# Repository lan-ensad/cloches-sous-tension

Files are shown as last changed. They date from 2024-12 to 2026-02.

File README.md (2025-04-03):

# cloches sous tensions

<!-- TOC -->
- [1. How it works](#1-how-it-works)
    - [1.1. General hardware diagram](#11-general-hardware-diagram)
    - [1.2. General software diagram](#12-general-software-diagram)
- [2. Programm usage](#2-programm-usage)
    - [2.1. Two modes](#21-two-modes)
    - [2.2. Config.yaml](#22-configyaml)
    - [2.3. Class & Functions](#23-class--functions)
        - [2.3.1. sol](#231-sol)
        - [2.3.2. recorder](#232-recorder)
        - [2.3.3. player](#233-player)
        - [2.3.4. utils](#234-utils)
- [3. Electronic](#3-electronic)
    - [3.1. Components](#31-components)
    - [3.2. PCB layout](#32-pcb-layout)
    - [3.3. Wiring](#33-wiring)
- [4. MIDI hardaware](#4-midi-hardaware)
- [5. 3D Modeling](#5-3d-modeling)
- [6. Non-tested modifications](#6-non-tested-modifications)
- [7. Known bugs](#7-known-bugs)
- [8. V2 expected](#8-v2-expected)
- [9. Maintenance, update](#9-maintenance-update)
- [10. Hardware limitations](#10-hardware-limitations)
<!-- /TOC -->

***

This project was born in collab with [Francois Dufeil](https://francoisdufeil.com/) and his sculptural works. 

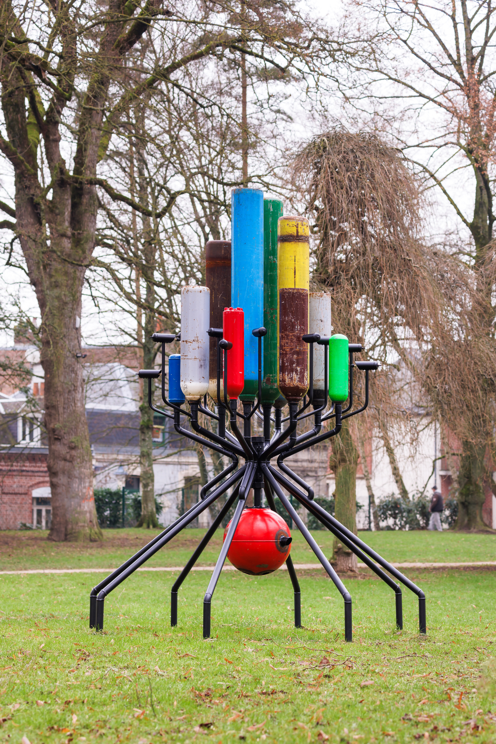
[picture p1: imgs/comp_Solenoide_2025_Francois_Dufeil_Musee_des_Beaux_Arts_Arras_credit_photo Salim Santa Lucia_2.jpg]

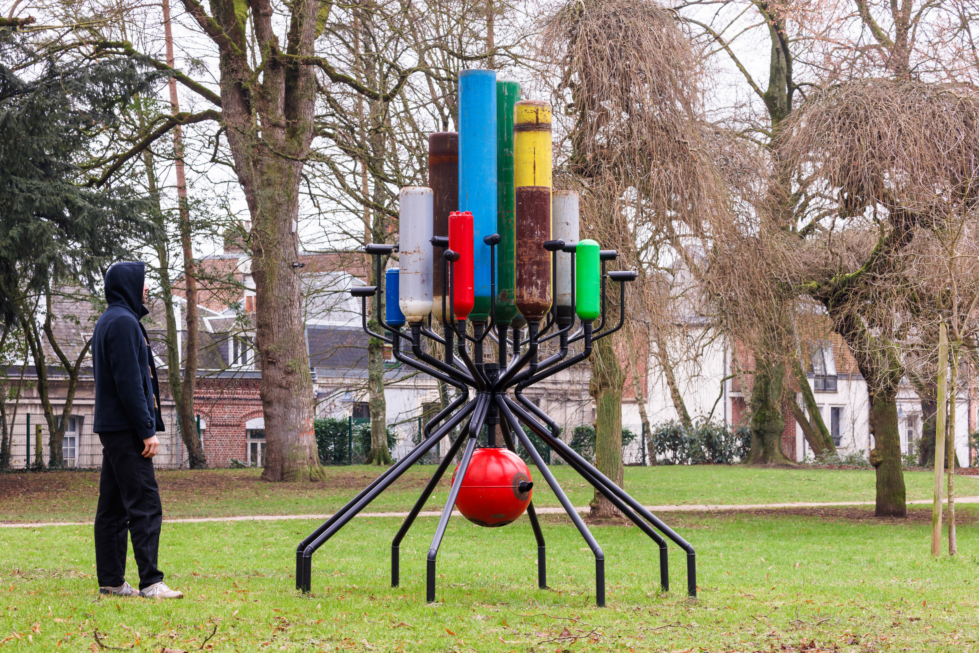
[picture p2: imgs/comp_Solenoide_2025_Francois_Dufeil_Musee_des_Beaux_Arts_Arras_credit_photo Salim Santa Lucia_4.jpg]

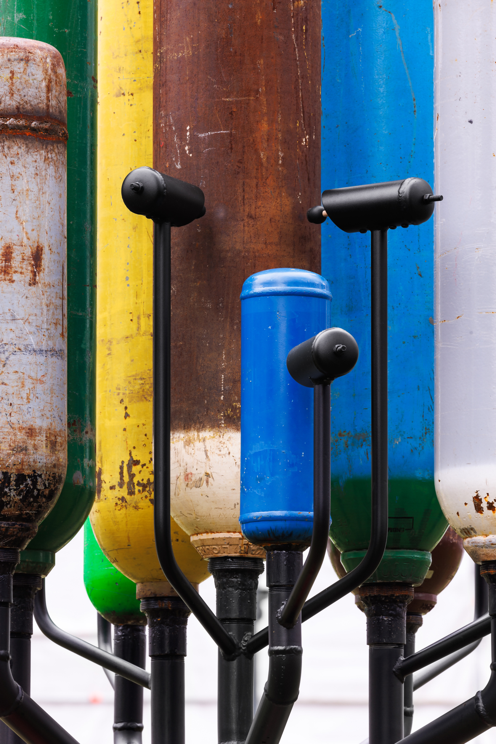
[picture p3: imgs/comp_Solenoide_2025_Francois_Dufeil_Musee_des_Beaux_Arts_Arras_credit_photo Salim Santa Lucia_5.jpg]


**Video :**\
video (https://www.youtube.com/watch?v=u8s93TluLmw)

photo @[Salim Santa Lucia](http://salimsantalucia.com/)

It uses a raspberry PCA9685 shield and 16 solenoides ITS-LS3830BD and homemade pcbs with a mosfet type IRL540. The goal is control accuratly the velocity of the impact between motors and bells to be able to play *forte* and *piano*.

Python main script runs `@reboot` in the `crontab` system.

## 1. How it works

### 1.1. General hardware diagram

hardware

### 1.2. General software diagram

software

## 2. Programm usage

### 2.1. Two modes

- **live** 
    - activate solenoides with a midi crontoller
    - in `config.yaml` you can set :
        - `message.note`\
            to map the midi note of the controller
        - `message.velocity`\
            it use the velocity to trigg the mosfet
        - record a score. Note that the score is not recorded in .midi but in .txt (cf.[Class & Functions](#class--functions)>**recorder**)
        - `message.control_change`\
            to map the control_change note (cf.[Class & Functions](#class--functions)>**`toggle_drony()`**)
    - for the happening \
    more details : [MIDI hardware](#midi-hardaware)
        - Arturia KeyStep Pro → MIDI out
        - MIDI in → Arturia BeatStep Pro
    - do not care about `message.channel` or `message.time`
- **auto**
    - read a score at the boot (cf.[Class & Functions](#class--functions)>**utils**>**`draw_lottery()`** and **`many_lottery()`**)
    - in `config.yaml` `date` where can set the range and the number of `draw_lottery()` defines in `utils.py`
    - when auto mode is triggered, `handle_score()` will read at once a score. After the `first_playing_score` is set to False and the function wait `now() == target()` to read the next score store in table_draw
    - `table_draw` is define with the `utils.many_draw(x)` function where x is the number of auto will be triggered

### 2.2. Config.yaml

|function|description|
|--|--|
|**controller**|simply the name of the controller. You can use `available_ports()` function in `utils.py` to get the exacte name.|
|**date**|usefull to set the range of hours to trigger the automation, the number of time of activation|
|**signal**|define the range of value (7bits for midi input and 16bits for PWM signal) and sommes default value when drony is triggered|
|**PWM**|settings for the PCA9685 shield|
|**mapping**|collection of midi notes and control_change to map the PWM channel of the PCA9685|
|**machine**|specifications of the machine (motors, btn_pin, led_pin) AND the `travel_time` table wich defines the `hit_length` of solenoides depending of the `message.velocity`|

### 2.3. Class & Functions

#### 2.3.1. sol

Main class based on asyncio

|function|description|
|--|--|
|**tape()**|It automaticly set the travel_time `self.hit_length` by searching in the config.yaml at machine->motors->travel_time| 
|**toggle_drony()**|When call, it create an async task `self.drony()` or cancels it if `self.dronying` is True. It free some bandwith for the midi signal and you can set the time between two tapes with the `midi.control_change.value` into the `stream_potard()`|
|**drony()**|**Do not call by itself**. The security heat setting is comments, ad the frequency calculator. the `self.delai_off` is set with the `self.stream_potar()` function|
|**get_timer()**|It uses by security settings as well as frequency calculator|

#### 2.3.2. recorder

|function|description|
|--|--|
|**get_current_millis()**|the recorder needs to know the duration between two midi note. Only 1ms definition|
|**write()** and **record()**|realy simple and automated. You can call the `rec.record_score()` in each loop, it will record as the `rec.record_status == True` and stop when is False.|

You can take a look at the `handle_score()` in `main.py` or `recorder.py`.

This is a sample of recorder looks like :
```
450
note_on channel=0 note=67 velocity=40 time=0
106
note_off channel=0 note=67 velocity=64 time=0
387
note_on channel=0 note=68 velocity=100 time=0
```
#### 2.3.3. player

|function|description|
|--|--|
|**read_file()**|load a score in `self.raws`|
|**parse_midi_string()**|use the mido `Message()` function to return the line's score into a midi message|

The `handle_score()` in `main.py` parse the file line by line to consider odds line with the delay between to midi messages.

#### 2.3.4. utils
Collection of functions

|function|description|
|--|--|
|**pca**|Usefull to use the driver just by calling `utils.pca.*<any_functions>*`|
|**draw_lottery()** and **many_lottery()**|Theses functions read how many `.txt` are in the root folder to set the table_draw list|
|**reset_all_pwn()**|Pretty secure to avoid any locked in solenoide at every boot|
|**available_ports()**|You can know the exacte name of your midi controller|
|**connecting_controller()**|Async function to let user switch the machine state before or after the keyboard pluged|

## 3. Electronic

### 3.1. Components

- RaspberryPi 4 with a [PCA9685 shield](https://www.waveshare.com/wiki/Fan_HAT)\
I only use it for the PCA9685 chip controlled I2C
    - installation
    ```
    sudo apt update && sudo apt upgrade
    sudo apt install python3-pip python3-smbus
    sudo pip install RPi.GPIO
    ```
- [Button](https://www.gotronic.fr/art-bouton-poussoir-ip67-bt22b-l-v-34105.htm) to switch live/auto mode
- [Emergency stop button](https://www.amazon.fr/gp/product/B097B8S6XL/ref=ox_sc_act_title_1?smid=A066248065M1IW1TJ2D&psc=1) connect only on the 48Volt power supply
- 12V and 48V power supply. 12V for the Raspberry and 48V (we chose 420W) for the solenoides.

### 3.2. PCB layout

You can find the KiCad projet, .svg and .step in `pcb_design/_src` folder. I chose the irl540 mosfet to design the regulator. 

- Schem
schem

- Layout
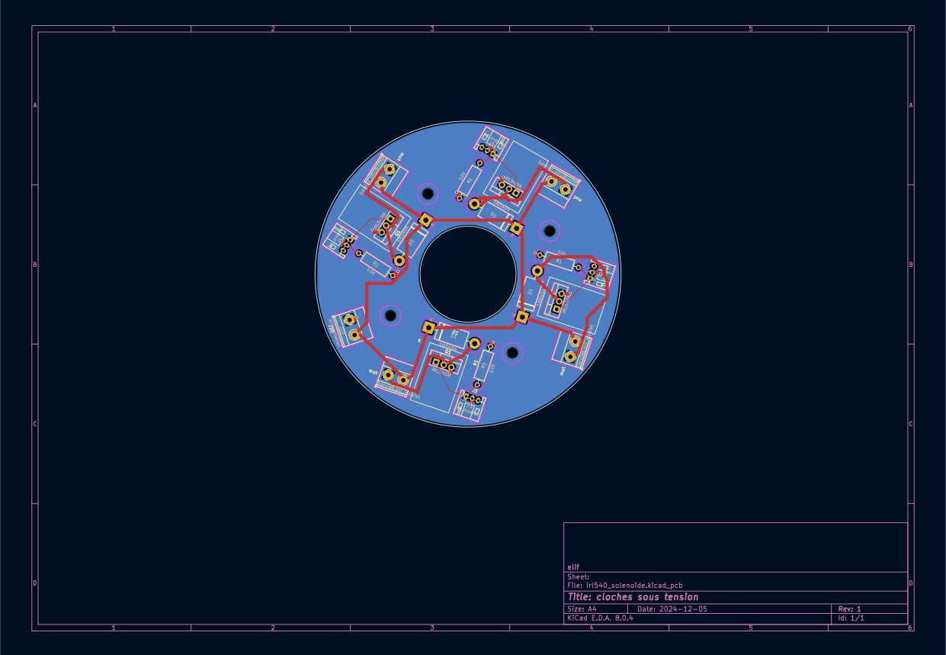
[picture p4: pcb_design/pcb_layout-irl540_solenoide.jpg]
layout

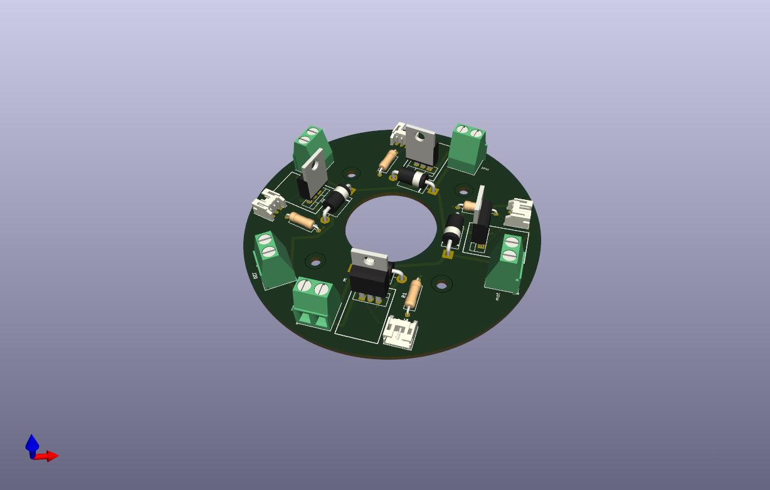
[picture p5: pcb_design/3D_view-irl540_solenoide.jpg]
schem


### 3.3. Wiring

- 16 pwm output from the pca9685 shield on the irl540 pcb with the common rapsberry and shield GND
- button\
you can find all in `config.yaml`:`machine`
    - GPIO27 : pullup pin
    - GPIO17 : led pin
    - the GND is common

wiring

## 4. MIDI hardaware

- [BeatStep Pro](https://www.arturia.com/fr/products/hybrid-synths/beatstep-pro/resources) made by Arturia. This is the master keyboard connected to the Raspberry Pi. You can download the Midi Control Center to map all the keys and match it in `config.yaml`.
- [KeyStop Pro](https://www.arturia.com/fr/products/hybrid-synths/keystep-pro/resources) made by Arturia. We use it to send midi notes and play with all the features — record sequences, arpeggiators, pattern, scaling, arranging... — This keyboard is really easy to use and very versatil.

keyboad-connections

## 5. 3D Modeling

You can find some parts that we use to properly mount the brain inside the box.

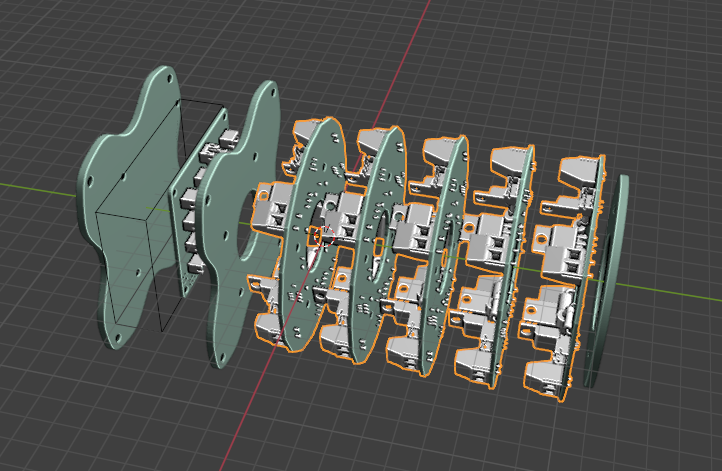
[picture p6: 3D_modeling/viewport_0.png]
viewport


## 6. Non-tested modifications

- time-mapping in microsecond instead milliseconds
    - drasticly reduce the queue time
    - more convient with live mode and recording mode
- disable the first delay in the recorder
- change toggle_drony() to activate_drony() and stop_drony()\
    more stable and accurate to the note_on or note_off midi signal

## 7. Known bugs

- sometimes the recorder apply a 10 or 100 factore to the delay between two midi signal

## 8. V2 expected

- add redis server to catch and possibly change some values
- add logging
- separate all functions
    - live
    - routine
    - reading
- add node-red interface
    - select score to play
    - file system to explore the recorded scores
- change temporale structure mapping
- improve BTN{}
    - get_state()
    - callback when trigger
- improve Player{}
    - add sol inside
    - player.read(), player.stop()...

## 9. Maintenance, update

For the software maintenance and modify some scores the raspberry is connected to my VPN so I have ssh access to modify, reboot, update, upgrade...

## 10. Hardware limitations

- Because MIDI send 7bits values and the PCA9685 use 16bits value, consider to use the `utils.convert()` function.
- `['machine']` section in the `config.yaml`
    - *btn_pin* and *led_pin* to set a visual indication switch *live<->auto* mode
    - *travel_time*\
    the solenoide needs time to reach the bells's contact point. This travel time (named `hit_length` sometimes in the code) is define by the PWM value sended (`message.velocity`).\
    The formula `int((1100*(pow(3.14,(-0.055*p))))+23)` suppose to give the best result where `p` is the `message.velocity` but I failed to implement it correctly because of latency issues.\
    So the travel_time manages a manuel mapping with the `utils.find_index()` and the `travel_time` table in `config.yaml`
- solenoide
    - security setting `max_dronying` exist but i finaly disable it in the exhibition version cause i did not notice too much heat during tests phase of the prototype. In addition sometimes it produces an axe drifting effect that is pretty satisfying and creates some cool patterns wich are not possible with the setting enable and the frequency of hit drasticly improve with `self.d.off`<15ms

 <p xmlns:cc="http://creativecommons.org/ns#" xmlns:dct="http://purl.org/dc/terms/"><a property="dct:title" rel="cc:attributionURL" href="https://github.com/lan-ensad/cloches-sous-tension">cloches sous tensions</a> by <a rel="cc:attributionURL dct:creator" property="cc:attributionName" href="https://github.com/lan-ensad">Olivier Bienz</a> is licensed under <a href="https://creativecommons.org/licenses/by-nc-sa/4.0/?ref=chooser-v1" target="_blank" rel="license noopener noreferrer" style="display:inline-block;">CC BY-NC-SA 4.0</a></p>

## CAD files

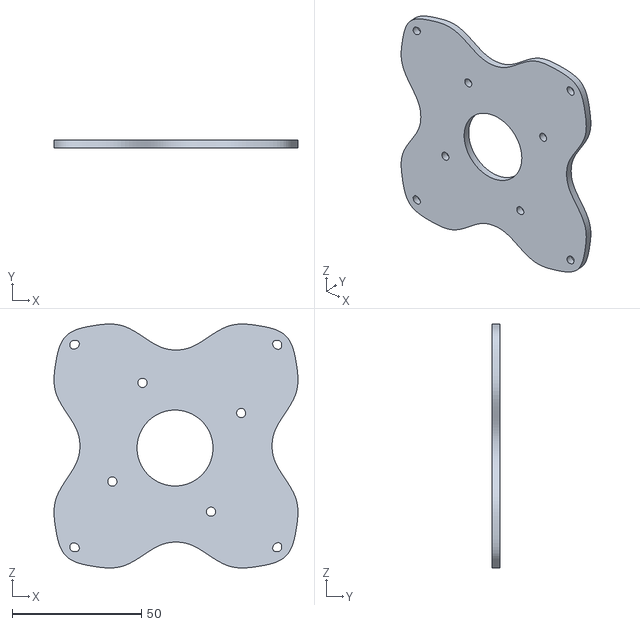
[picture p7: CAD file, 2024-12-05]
3D_modeling/_print/mosfet_mount.stl
94.5 x 3.00 x 94.5

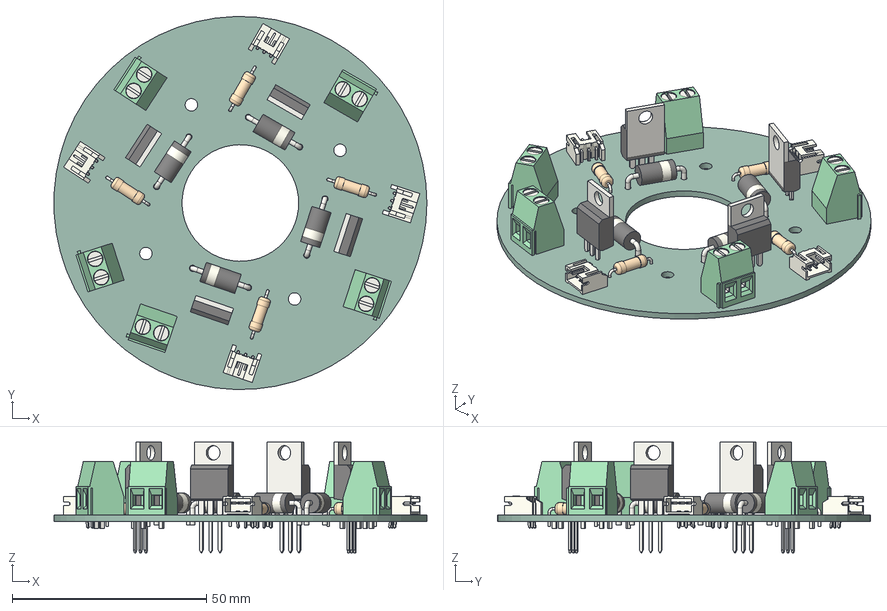
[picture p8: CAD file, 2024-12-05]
pcb_design/3D_model-irl540_solenoide.step
95.9 x 96.0 x 28.5 mm
D_DO-201AD_P15.24mm_Horizontal x 4
TO-220-3_Vertical x 4
JST_S3B_PH_K x 4
R_Axial_DIN0309_L90mm_D32mm_P1270mm_Horizontal x 4
TerminalBlock_Phoenix_MKDS_15_2_1x02_P500mm_Horizontal x 5
irl540_solenoide_PCB

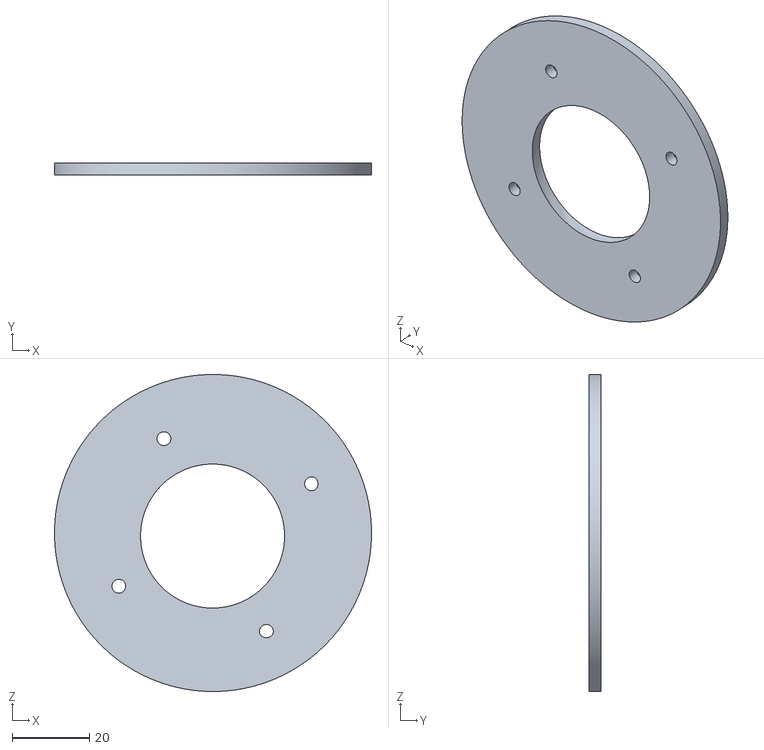
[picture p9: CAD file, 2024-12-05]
3D_modeling/_print/mosfet_end.stl
82.2 x 3.00 x 82.2

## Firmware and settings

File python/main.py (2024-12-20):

from sol import Sol
from recorder import Recorder
from player import Player
from btn import BTN
import utils
import time
import asyncio
import mido
import RPi.GPIO as GPIO
import os
import datetime

##           LOAD CONFIG
config = utils.yaml_load_config('config.yaml')
## ====================================
##             CONFIG
PADS_NOTES = config['mapping']['pads']
MOT_PIN = config['mapping']['sol']
DRONY_NOTES = config['mapping']['drony_sol_notes']
POTAR_CONTROL = config['mapping']['potar_control']
drony_status = [False]*config['machine']['nb_motors']
NUMBER_DRAW = config['date']['total_draw']
## ====================================
##            TRIGGER DRAW
table = [[10, 50], [12, 50], [13, 50], [15, 50]] ## ACTIVATION TIME
index_auto_playing = 0
## ====================================
##          SWITCH AUTO/LIVE
btn = BTN(config['machine']['switch_btn_pin'], config['machine']['led_state_pin'])
## ====================================
##          MOTORS PIN TABLES
sol = []
for i in range(len(MOT_PIN)):
    sol.append(Sol(MOT_PIN[i]))
## ====================================
##            REC FUNCTIONS
score_dir = os.path.dirname(os.path.abspath(__file__))
rec = Recorder('score')
rec.score_ID = utils.how_many_scores(score_dir)+1
first_score = "score_"+str(config['date']['first_score'])+".txt"
pl = Player()
## ====================================
##         MAIN STATE AUTO/LIVE
listen_midi = None
midi_controller = None
playing_score = None
first_playing_score = True
midi_connected = False

async def connecting_controller(port_name):
    global midi_connected
    global midi_controller
    global listen_midi
    while True:
        try:
            midi_controller = mido.open_input(port_name)
            midi_connected = True
            print(f'connected {midi_controller}')
        except (IOError, OSError):
            print(f'{port_name} not found... Retry in 1scd')
        else:
            with midi_controller as midi_in:
                listen_midi = asyncio.create_task(handle_event(midi_in))
                await listen_midi
        await asyncio.sleep(1)

async def switch_state():
    global listen_midi
    global playing_score
    global first_playing_score
    global index_auto_playing
    global midi_controller
    while True:
        if btn.state:
            ##      LIVE MODE
            if btn.prev_state!=btn.state:
                if playing_score is not None:
                    playing_score.cancel()
                    playing_score = None
                    utils.reset_all_pwm()
                await connecting_controller(config['controller']['name'])
                # print('live')
                btn.prev_state = btn.state
        else:
            ##      READ SCORE
            if btn.prev_state!=btn.state:
                if listen_midi is not None:
                    listen_midi.cancel()
                    listen_midi = None
                    utils.reset_all_pwm()
                ##      BOOT READ SCORE
                if first_playing_score:
                    print('first playing...')
                    time.sleep(180) # Wait before play the first score
                    playing_score = asyncio.create_task(handle_score("score_25.txt"))
                if not first_playing_score:
                    playing_score = asyncio.create_task(handle_score("score_25.txt"))
                btn.prev_state = btn.state
        await asyncio.sleep(0.01)

async def handle_score(sc: str):
    global first_playing_score
    global index_auto_playing
    played = False
    pl.read_file(sc)
    while True:
        if first_playing_score:
            for item in pl.raws:
                if item.isdigit():
                    delay = int(item)
                    await asyncio.sleep(delay/1000)
                else:
                    message = pl.parse_midi_string(item)
                    ### ===================================================
                    ###                     NOTE_ON
                    if message.type == "note_on":
                        ###   DRONYING
                        if message.note in DRONY_NOTES:
                            index = DRONY_NOTES.index(message.note)
                            if not sol[index].dronying: ## prevent axe shifting when dronying
                                await sol[index].toggle_drone(utils.convert(message.velocity), 250)
                                drony_status[index] = True
                                print(f'Activate sol drony {DRONY_NOTES.index(message.note)+1}')
                        ###   ONT TAPE 
                        if message.note in PADS_NOTES :
                            index = PADS_NOTES.index(message.note)
                            if not drony_status[index]:
                                await sol[index].tape(utils.convert(message.velocity))
                                print(f'cloche n°{PADS_NOTES.index(message.note)+1} at {message.velocity} travel time: {sol[PADS_NOTES.index(message.note)].hit_length}')
                    ### ===================================================
                    ###                     NOTE_OFF
                    if message.type == "note_off":
                        if message.note in DRONY_NOTES:
                            index = DRONY_NOTES.index(message.note)
                            await sol[index].toggle_drone()
                            drony_status[index] = False
                            print(f'Deactivate sol drony {DRONY_NOTES.index(message.note)+1}')
                    ### ===================================================
                    ###                 CONTROL CHANGE
                    if message.type=="control_change":
                        if message.control in POTAR_CONTROL:
                            index = POTAR_CONTROL.index(message.control)
                            if drony_status[index]:
                                sol[index].stream_potar(utils.map_val(message.value, 0, config['signal']['input_max'], config['signal']['drony_min'], config['signal']['drony_max']))
            first_playing_score = False
            utils.reset_all_pwm()
        else:
            utils.reset_all_pwm()
            now = [datetime.datetime.now().hour, datetime.datetime.now().minute]
            target = table[index_auto_playing]
            print(f'Waiting next alignement | now:{now}\ttarget:{target}')
            if now[0]>target[0]:
                index_auto_playing +=1
                print('index +1')
            elif now[0]==target[0] and now[1]>target[1]:
                index_auto_playing +=1
                print('index +1')
            elif now == target:
                if not played :
                    for item in pl.raws:
                        if item.isdigit():
                            delay = int(item)
                            await asyncio.sleep(delay/1000000)
                        else:
                            message = pl.parse_midi_string(item)
                            # print(message)
                            ### ===================================================
                            ###                     NOTE_ON
                            if message.type == "note_on":
                                ###   DRONYING
                                if message.note in DRONY_NOTES:
                                    index = DRONY_NOTES.index(message.note)
                                    if not sol[index].dronying: ## prevent axe shifting when dronying
                                        await sol[index].toggle_drone(utils.convert(message.velocity), 250)
                                        drony_status[index] = True
                                        print(f'Activate sol drony {DRONY_NOTES.index(message.note)+1}')
                                ###   ONT TAPE 
                                if message.note in PADS_NOTES :
                                    index = PADS_NOTES.index(message.note)
                                    if not drony_status[index]:
                                        await sol[index].tape(utils.convert(message.velocity))
                                        print(f'cloche n°{PADS_NOTES.index(message.note)+1} at {message.velocity} travel time: {sol[PADS_NOTES.index(message.note)].hit_length}')
                            ### ===================================================
                            ###                     NOTE_OFF
                            if message.type == "note_off":
                                if message.note in DRONY_NOTES:
                                    index = DRONY_NOTES.index(message.note)
                                    await sol[index].toggle_drone()
                                    drony_status[index] = False
                                    print(f'Deactivate sol drony {DRONY_NOTES.index(message.note)+1}')
                            ### ===================================================
                            ###                 CONTROL CHANGE
                            if message.type=="control_change":
                                if message.control in POTAR_CONTROL:
                                    index = POTAR_CONTROL.index(message.control)
                                    if drony_status[index]:
                                        sol[index].stream_potar(utils.map_val(message.value, 0, config['signal']['input_max'], config['signal']['drony_min'], config['signal']['drony_max']))
                ### ===================================================
                ###                 AFTER PLAYED SCORE
                index_auto_playing+=1 ## wait the next trigger time
                utils.reset_all_pwm()
        await asyncio.sleep(1) ## Testing alignement every 1 scd

async def handle_event(midi_in):
    while True:
        message = midi_in.poll()
        if message:
            # print(str(message))
            if message.type != 'sysex':
                rec.record_score(str(message))
            ### ===================================================
            ###                 CONTROL CHANGE
            if message.type == 'control_change':
                ###   RECORD CONTROL
                if message.control == config['mapping']['rec']:
                    if message.value == config['signal']['input_max'] :
                        rec.record_status = True
                    else :
                        rec.record_status = False
                        rec.score_ID +=1
                if message.control in POTAR_CONTROL:
                    index = POTAR_CONTROL.index(message.control)
                    if drony_status[index]:
                        sol[index].stream_potar(utils.map_val(message.value, 0, config['signal']['input_max'], config['signal']['drony_min'], config['signal']['drony_max']))
            ### ===================================================
            ###                     NOTE_OFF
            if message.type == 'note_off':
                if message.note in DRONY_NOTES:
                    index = DRONY_NOTES.index(message.note)
                    await sol[index].toggle_drone()
                    drony_status[index] = False
                    print(f'Deactivate sol drony {DRONY_NOTES.index(message.note)+1}')
            ### ===================================================
            ###                     NOTE_ON
            if message.type == 'note_on':
                ###   DRONYING
                if message.note in DRONY_NOTES:
                    index = DRONY_NOTES.index(message.note)
                    if not sol[index].dronying: ## prevent axe shifting when dronying
                        await sol[index].toggle_drone(utils.convert(message.velocity), config['signal']['drony_start'])
                        drony_status[index] = True
                        print(f'Activate sol drony {DRONY_NOTES.index(message.note)+1}')
                ###   ON TAPE 
                if message.note in PADS_NOTES :
                    index = PADS_NOTES.index(message.note)
                    if not drony_status[index]:
                        await sol[index].tape(utils.convert(message.velocity))
                        print(f'cloche n°{PADS_NOTES.index(message.note)+1} at {message.velocity} travel time: {sol[PADS_NOTES.index(message.note)].hit_length}')
            ## ===================================================
        await asyncio.sleep(0.000001)

async def main():
    utils.reset_all_pwm()
    listen_btn = asyncio.create_task(btn.read_state())
    listen_switch = asyncio.create_task(switch_state())
    await listen_btn
    await listen_switch

asyncio.run(main())

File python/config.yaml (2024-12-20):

controller:
  name: Arturia BeatStep Pro:Arturia BeatStep Pro Arturia Be 28:0

date:
  ### NOT USE IN EXHIBITION STATE ###
  # hour_range: [10, 17]
  # minute_range: [0, 59]
  # total_draw: 3
  ###################################
  first_score: 1

signal:
  input_min: 0
  input_max: 127  ## MIDI_6bits
  output_min: 0
  output_max: 65535 ##16bits channel
  drony_start: 263
  drony_max : 555
  drony_min : 3

PWM:
  clock: 25000000 ## default 25000000 | lowest 1000000
  freq: 50 ## 50Hz -> EU | lowest 1Hz@clock-lowest

mapping:
  potar_control: [20,21,22,23,24,25,26,27,28,29,30,31,46,47,52,53] ## midi control_change
  drony_sol_notes: [0,1,2,3,4,5,6,7,8,9,10,11,12,13,14,15] ## midi note sol.dronying activation
  pads: [60,61,62,63,64,65,66,67,68,69,70,71,72,73, 74,75] ## midi note sol.tape()
  rec: 50 ## midi note
  stop: 51 ## midi note
  sol: [5,6,7,3,15,10,2,14,8,0,4,11,13,1,12,9] ## pwm pin - PCA9685

machine:
  nb_motors: 16
  switch_btn_pin: 27
  led_state_pin: 17 
  travel_time:
  - [250,200,180,150,135,120,115,110,105,100,95,90,85,75,70,65,55,50,45,40,35,30,25,20,15]

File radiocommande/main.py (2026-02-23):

# main.py -- put your code here!
from machine import Pin
from umqttsimple import MQTTClient
import time

# Configuration MQTT
MQTT_BROKER = "192.168.1.102"  # Adresse IP du broker MQTT
MQTT_TOPIC = b"instants/rc"
CLIENT_ID = "esp32_rc"

# Configuration bouton
BUTTON_PIN = 1

# Initialisation du bouton avec pull-up interne
button = Pin(BUTTON_PIN, Pin.IN, Pin.PULL_UP)

# État précédent du bouton (pour détecter le front descendant)
last_state = 1
playing = 0

def connect_mqtt():
    set_led("connecting mqtt")
    client = MQTTClient(CLIENT_ID, MQTT_BROKER)
    client.connect()
    print("MQTT connecté au broker", MQTT_BROKER)
    return client

def main():
    global last_state, playing

    print("Connexion MQTT...")
    client = connect_mqtt()
    set_led("ready")

    print("En attente d'appui sur le bouton (GPIO {})...".format(BUTTON_PIN))

    while True:
        current_state = button.value()

        # Détection front descendant (bouton pressé, pull-up donc 1->0)
        if last_state == 1 and current_state == 0:
            set_led("sending msg")
            print("Bouton pressé! Envoi 'play'...")
            if playing==0:
                client.publish(MQTT_TOPIC, b"play")
                playing = 1
            elif playing==1:
                client.publish(MQTT_TOPIC, b"stop")
                playing=0
            print("Message envoyé!")

        last_state = current_state
        time.sleep_ms(200)  # Anti-rebond
        set_led("ready")
    time.sleep_ms(10)

main()
